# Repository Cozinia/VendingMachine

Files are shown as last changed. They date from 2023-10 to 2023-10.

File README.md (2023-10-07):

# Vending Machine

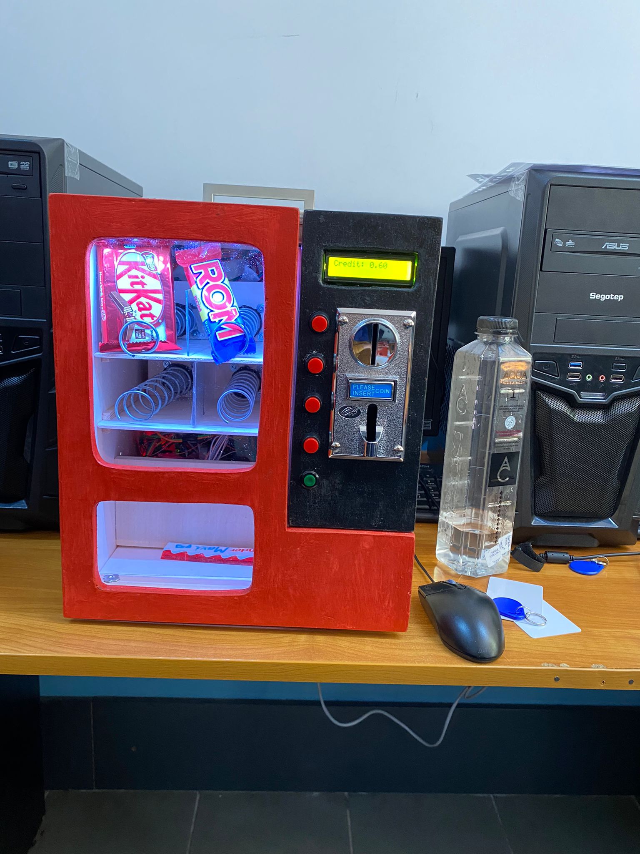
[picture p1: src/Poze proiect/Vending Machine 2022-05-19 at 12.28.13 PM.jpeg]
VendingMachinePhoto


## Descrierea componentelor folosite

În cadrul acestui proiect voi fi folosite mai multe componente așa că mai jos se află  o mică prezentare a acestora și cum sunt legate la microcontroler.
### Numărătorul de monede
Primul pe ordinea de idei este numărătorul de monede, `CH-926` pe numele de cod, acesta acceptă până la 3 tipuri diferite de monede. 
Acest modul trebuie conectat la o sursă de 12V , iar pinul ce se ocupă cu transmiterea mesajului de identificare a monedelor trebuie conectat la unul dintre pinii digitali ai microcontroler-ului ca în schema de mai jos.

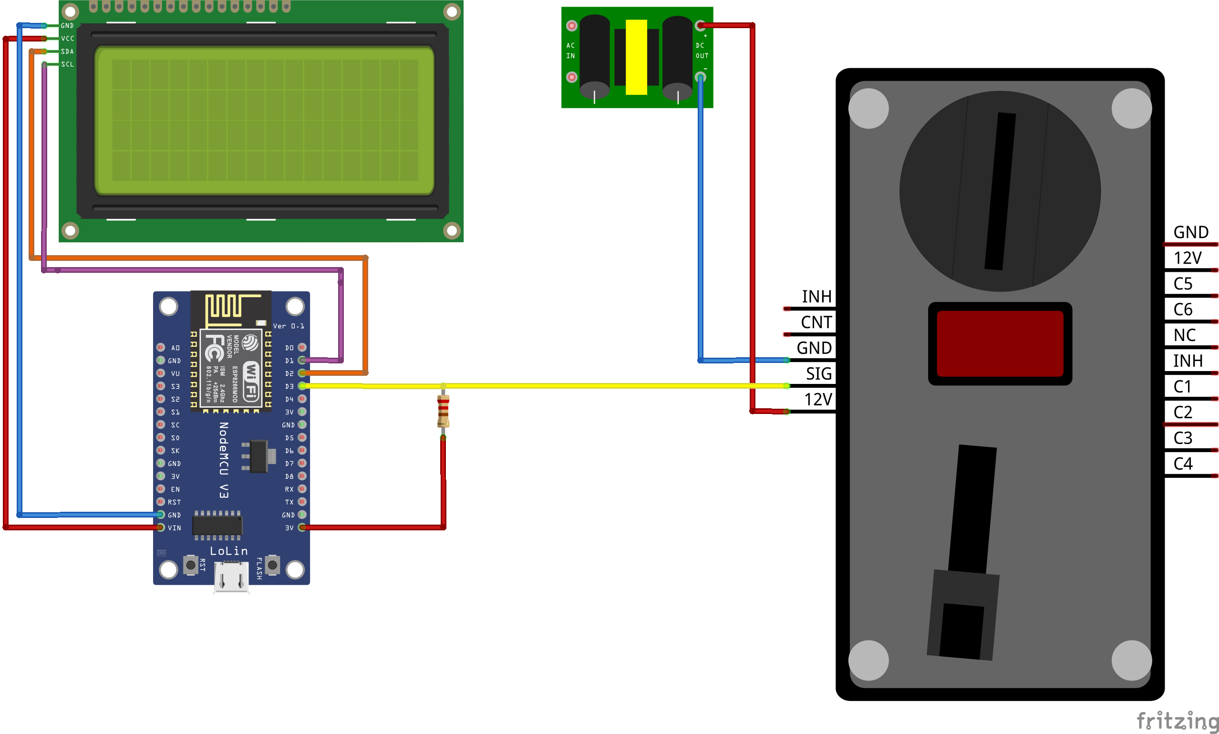
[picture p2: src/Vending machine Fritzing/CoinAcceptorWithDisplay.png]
CoinAcceptorWithDisplay


În desen se observă microcontroler-ul în partea stângă, sursa de 12V în partea de sus și numărătorul de monede în partea dreaptă.Acesta este conectat la sursa externă de 12V prin cele două fire(roșu pentru VCC și albastru pentru GND), iar prin firul de culoare galbenă la `ESP8266`, mai exact la 3V3 ce unește printr-un tranzistor pinul SIG(Coin) al acceptorului de monede cu pinul digital D3 al plăcuței.

Modulul este progrmat pentru a distinge 3 monede diferite(de `5, 10 și 50 bani`).Acesta se bazează pe pulsuri consecutive pentru fiecare tip de monedă în parte(un puls pentru 5 bani, două pulsuri pentru 10 bani, trei pulsuri pentru 50 de bani).

Iată câteva secvențe de cod interesante:

```
attachInterrupt(digitalPinToIntrerrupt(CoinPin), CoinEvent, CHANGE);
```
 
Pentru a nu supraîncărca plăcuța cu citiri successive se folosește attachInterrupt, metodă cu ajutorul căreia funcția CoinEvent este invocată doar la detectarea introducerii unei monede.
  
```
void CoinEvent()
{
    crtValue = digitalRead(CountPin);

    Serial.print("CoinEVENT_____________");
    Serial.print("\n");
    Serial.print(crtValue);
    Serial.print("\n");

}

```

`digitalRead` citește valoarea pinului Count și o stochează în variabila `crtValue`.

Funcția `Coins` se apelează în loop. Dacă timpul curent este diferit de cel anterior iar valoarea curentă de cea anterioară, timpul anterior ia valoarea celui prezent și valoarea anterioară ia valoarea celei prezente. Variabila de tip bool  numită changed își schimbă valoarea în true când această condiție este îndeplinită.Dacă diferența dintre timpul curent  și cel anterior este mai mare de 30 de milisecunde, iar changed este true, variabila number crește cu o unitate.

```
void Coins()
{
    //take current time
    crtTime = millis();
    //compare current time with previous time
    if (crtTime > prevTime)
    {
        //compare current value with previous value
        if (crtValue != prevValue)
        {
            prevTime = crtTime;

            prevValue = crtValue;
            changed = true;
        }
        if (crtTime - prevTime > 30 && changed)
        {
            counter++;
            Serial.print(counter);
            Serial.print("\n");
            changed = false;
            number++;
            Time1 = millis();
            changed = false;
        }
    }
    Time2 = millis();
    if ((Time2 - Time1 > TIMER) && (number))
    {

        Serial.print("Number: ");
        Serial.print(number);
        Serial.print("\n");
        Serial.print("Time2-Time1: ");
        Serial.print(Time2 - Time1);
        Serial.print("\n");

        if (number == 3)
        {
            credit = credit + 0.50;
            totalCoins3++;
            number = 0;
        }
        else if (number == 2)
        {
            credit = credit + 0.10;
            totalCoins2++;
            number = 0;
        }
        else
            if (number == 1)
            {
                totalCoins1++;
                credit = credit + 0.05;
                number = 0;
            }
        lcd.setCursor(0, 0);
        lcd.print("Credit: ");
        lcd.setCursor(8, 0);
        lcd.print(credit);
        Serial.print("Credit: ");
        Serial.print(credit);
        Serial.print("\n");
    }
}

```

În funcție de valoarea variabilei number, aceasta îndeplinește una dintre condițiile de mai sus.În acest fel creditul crește cu o anumită valoare(5, 10 sau 50 de bani), valoarea number este resetată la 0, iar variabila totalCoins crește cu o unitate pentru a înregistra numărul total de monede de un anumit tip.

### Display-ul

După punerea în funcțiune a numărătorului de monede a fost adăugat și un display pe care să afișeze creditul inserat.Mai jos este inserată o schemă ce conține și display-ul.

CoinAcceptorWithDisplay

Display-ul comunică prin protocolul I2C cu microcontroler-ul. Pentru a face acest lucru posibil se conectează pinii D1 la SCL(reprezentat prin cablul de culoare mov), D2 la SDA(reprezentat prin cablul de culoare oranj), pinul VIN(cel care transportă curent de 5V) la VCC și GND la GND.

```
//YWROBOT
//Compatible with the Arduino IDE 1.0
//Library version:1.1

#include <Wire.h>

#include <LiquidCrystal I2C.h>

LiquidCrystal I2C lcd(@x27, 16, 2); // set the LCD address to @x27 for a 16 chars and 2 line display

void setup()
{
lcd.init(); // initialize the lcd
i // Print a message to the LCD's screen
 lcd.backlight();

lcd.setCursor(@, 0);
lcd.print(“Atestat 2022 by");
lcd.setCursor(@, 1);
lcd.print(“Cozinia Motronu™);

}

void loop()
{

}

```
 
Acest cod folosește librăria „`LiquidCrystal_I2C`”.După declararea directivelor preprocesor „`Wire`” și „`LiquidCrystal_I2C`” se inițializează obiectul lcd care se află la adresa 0x27.În funcția setup se inițializează `lcd`, `backlight` și se setează cursorul pe poziția linia 0 și coloana 0 pentru a scrie un mesaj, respectiv lini 1 și coloana 0 pentru continuarea mesajului.
Mai jos este inserată o poză cu  un mesaj afișat pe display.

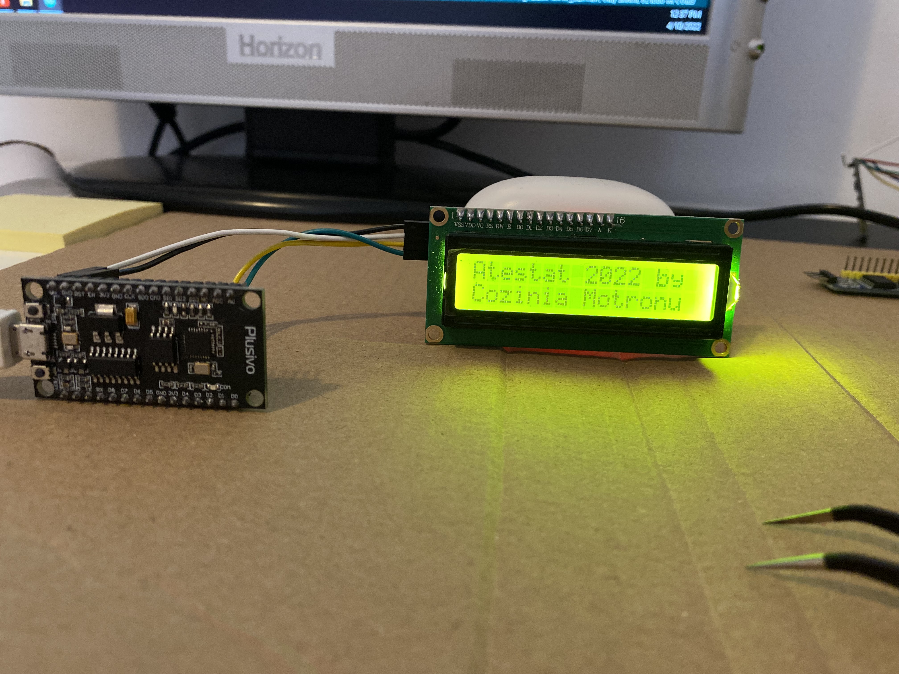
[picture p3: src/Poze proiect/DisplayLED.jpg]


### Motoarele

Acum schema începe să se încarce deoarece fiecare motor are 4 fire cu ajutorul cărora se conectează la shield-ul `CNC` și alte două care duc la modulul de expansiune `PCF8574`. Se folosesc aceste module deoarece atât motoarele, cât și celelalte componente ocupă foarte mulți pini și nu lasă loc disponibil pe microcontroler. `PCF8574` folosește același protocol precum display-ul, adică `I2C` pentru a transmite diferite evenimente ce se petrec pe pini.Acest lucru este convenabil deoarece se pot lega mai multe module de expansiune pentru a extinde numărul de pini.Aceste module se diferențiază prin adresă, fiecare putând fi programat manual ca având o anumită adresă(de la `0x20 la 0x27`) așa cum este ilustrat în imaginea de mai jos.

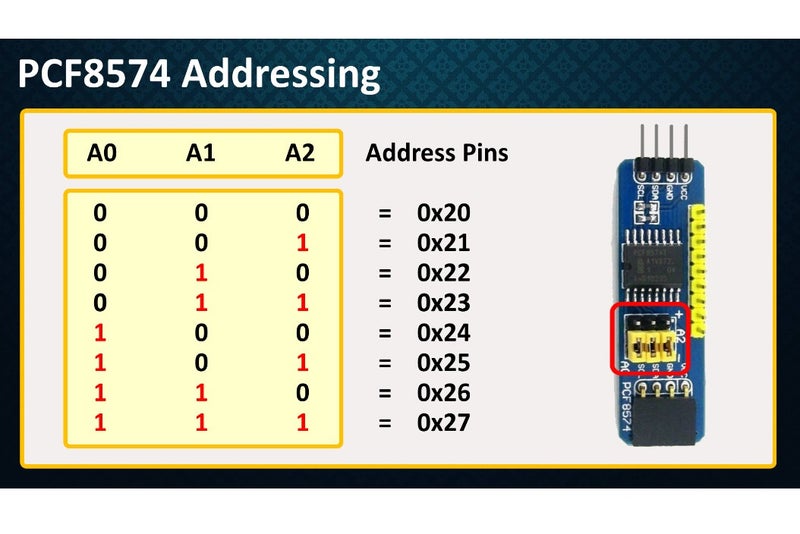
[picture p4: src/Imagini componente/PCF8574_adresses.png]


Shield-ul CNC împreună cu driver-ul de motoare `A4988` asigură buna funcționare a motoarelor oferind o interfață ușor de utilizat. 
Shield-ul oferă suport pentru maxim 4 drivere de motoare, un `pinEnable(EN)` pentru a activa mișcarea motoarelor, mai mulți pini de `ground(GND)`, pini care permit mișcarea motoarelor într-o anumită direcție și un anumit număr de pași, de exemplu: `X.STEP`(indică numărul de pași pe care motorul X să îl parcurgă), `X.DIR`(direcția în care să se învârtă motorul X). Shield-ul trebuie alimentat cu `12V` de la o sursă externă și 5V(curent necesar cerut de driver-ele de motoare).
	
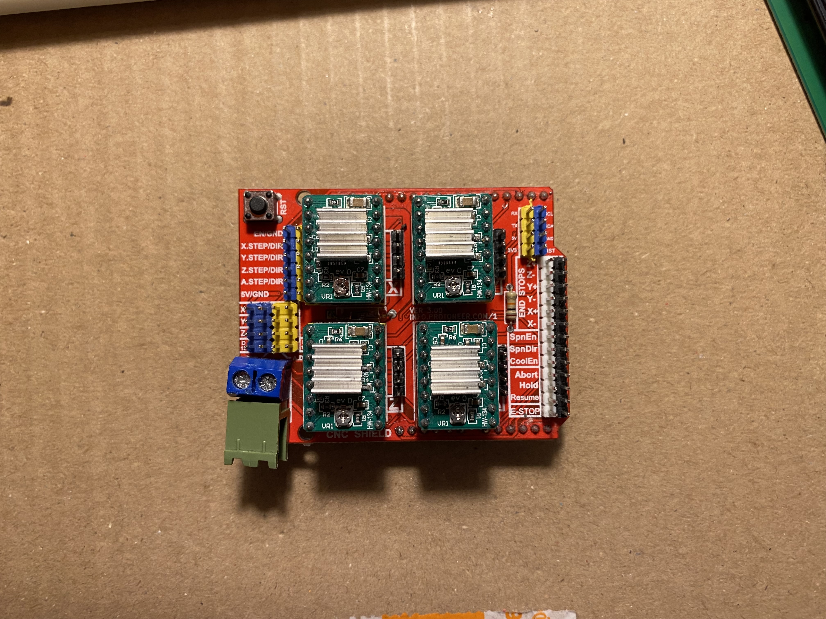
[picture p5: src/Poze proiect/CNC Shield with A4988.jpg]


Mai jos se poate observa schema proiectului la care se adaugăt motoarele, shield-ul cu driver-ele de motoare și modulele de expansiune a pinilor.

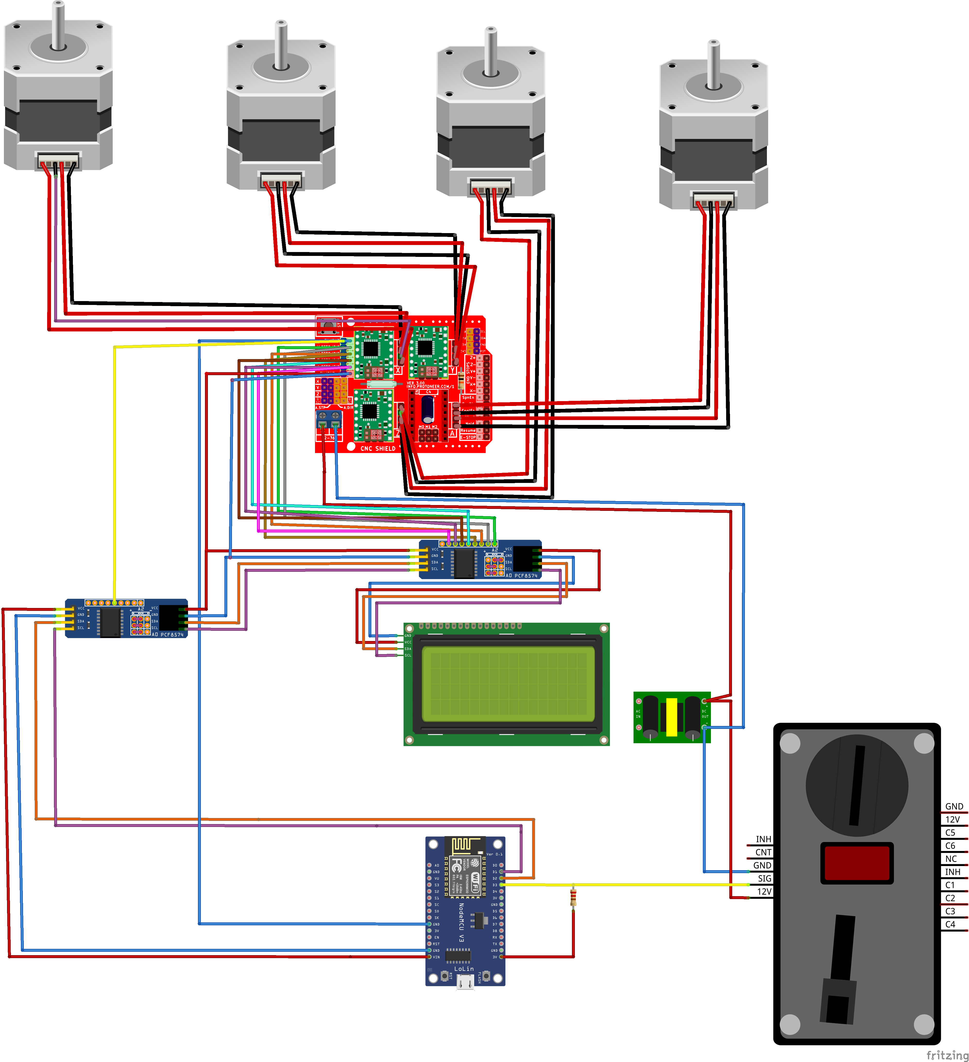
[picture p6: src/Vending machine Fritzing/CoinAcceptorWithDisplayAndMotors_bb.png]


### Modulul RFID

`RFID` este acronimul de la "radio-frequency identification" (identificare prin radiofrecvență) și se referă la o tehnologie prin care datele digitale codificate în etichete RFID sau etichete inteligente sunt captate de un cititor prin intermediul undelor radio. Tehnologia RFID este similară codului de bare, în sensul că datele de pe o etichetă sunt capturate de un dispozitiv care stochează datele într-o bază de date. Cu toate acestea, RFID are mai multe avantaje față de sistemele care utilizează un software de urmărire a activelor cu coduri de bare. Cel mai notabil este faptul că datele din etichetele RFID pot fi citite în afara liniei de vizibilitate, în timp ce codurile de bare trebuie aliniate cu un scaner optic.
Modul de utilizare este destul de simplu: utilizatorul  apropie cardul de scanner și datele sunt citite și prelucrate.În cazul acestui proiect utilizatorul folosește cardul pentru a se înregistra la vendomat, nemaifiind nevoie să introducă bani pentru a achiziționa produse.
Modulul RFID este conectat ca în schema de mai jos la pinii următori:

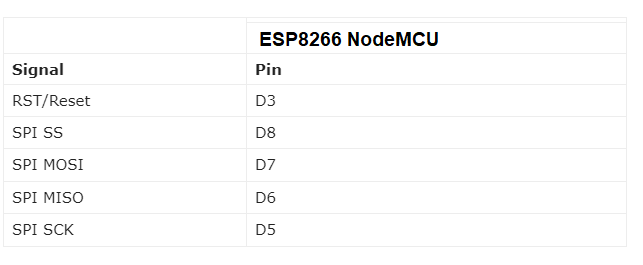
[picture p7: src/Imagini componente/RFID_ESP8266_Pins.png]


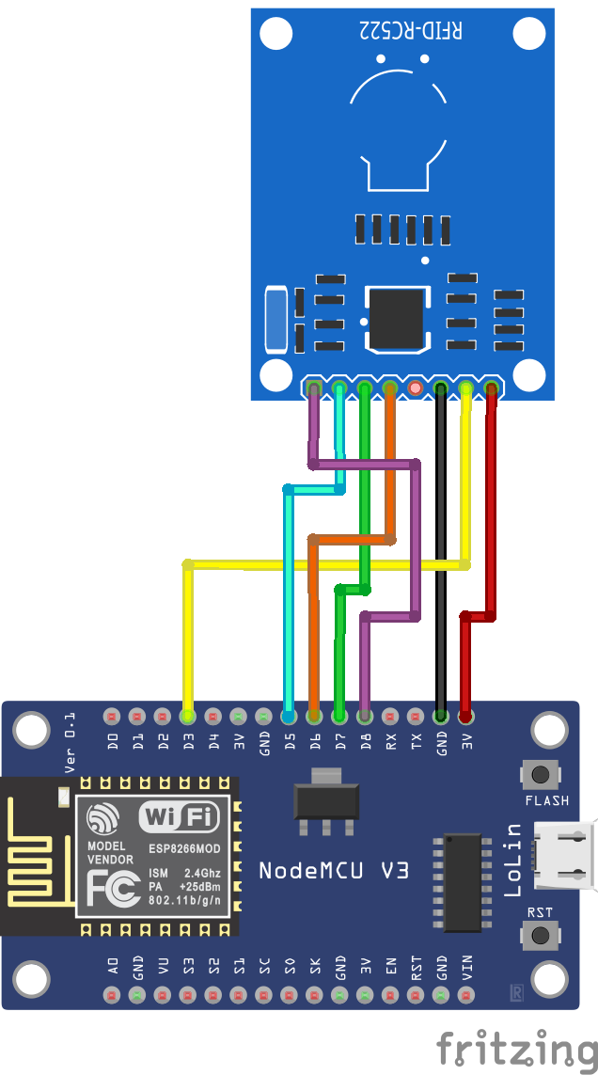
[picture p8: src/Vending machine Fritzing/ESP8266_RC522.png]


Pentru a putea folosi modulul RFID trebuie instalată librăria `MFRC522`.

Codul folosit este descris mai jos:
 
```
#include <SPI.h>
#include <MFRC522.h>

#define RST_PIN D3 // Configurable, see typical pin layout above
#define SS_PIN D8 // Configurable, see typical pin layout above
MFRC522 mfrc522(SS_PIN, RST_PIN); // Create MFRC522 instance

void setup()
{
Serial.begin(96060); // Initialize serial communications with the PC
SPI.begin(); // Init SPI bus
mfrc522.PCD_Init(); // Init MFRC522
mfrc522.PCD_DumpVersionToSerial(); // Show details of PCD - MFRC522 Card Reader details
Serial.println(F("Scan PICC to see UID, SAK, type, and data blocks..."));
}

void loop()
{
// Look for new cards
if (!mfrc522.PICC_IsNewCardPresent())
{
	return;
}
// Select one of the cards

if (!mfrc522.PICC_ReadCardSerial())
{
	return;
}
// Dump debug info about the card; PICC_HaltA() is automatically called

mfrc522.PICC_DumpToSerial(&(mfrc522.uid));

return;
}

```

După încărcarea acestui cod pe serială ar trebui să apară un mesaj asemănător cu cel de mai jos(mesajul poate să difere în funcție de versiunea moduluului RFID) unde puteți scana cardul.

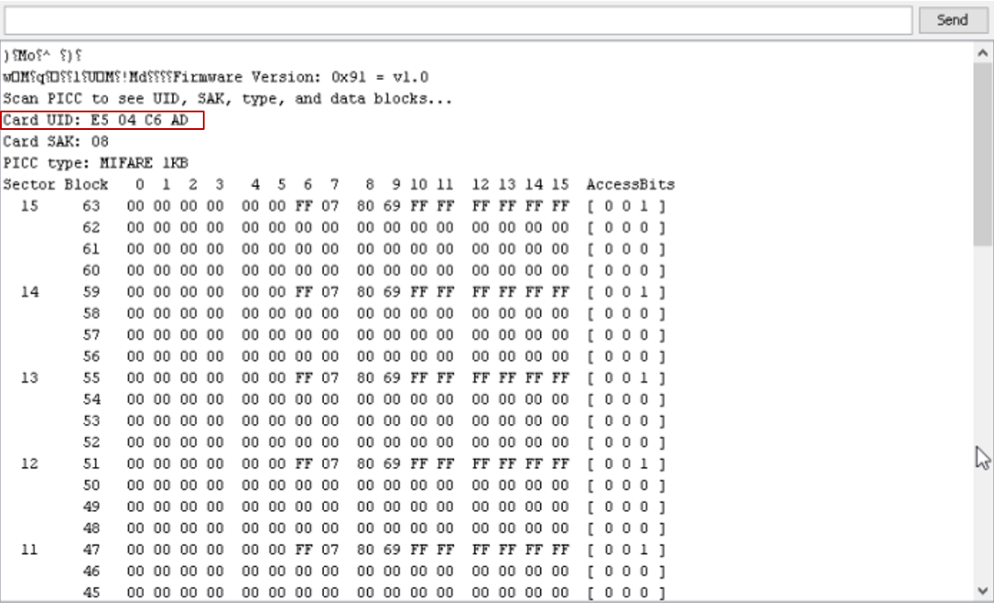
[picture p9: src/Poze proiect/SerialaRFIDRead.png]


Mai departe în implementarea codului care va identifica ID-ul cardului se va folosi „Card UID” .

### Stocarea datelor

Din cauza limitărilor spațiului de stocare pe care le au microcontroler-ele `ESP8266`(8MB RAM), nu este posibilă realizarea unei baze de date care să stocheze utilizatorii, produsele și tranzacțiile și în același timp să execute și comenzile celorlalte componente. În acest caz se folosesc structuri care imită tabelele enumerate mai sus.A cestea sunt realizate într-o clasă numită `FileDb`.

```
typedef struct
{
	char CNP[14];
	char FirstName[20];
	char Lastname[15];
	char Password[20];
	char TagNumber[15];
	float Credit;
	int isAdmin;
	int Enabled;

}User;
```

Această structură reține CNP-ul, nume, prenumele, parola, numărul cardului `RFID`, creditul, statutul utilizatorului(dacă este sau nu administrator) , iar parametrul Enabled are valoarea 1 dacă acesta este activ și 0 în caz contrar. Celelalte structuri arată similar.
După cum îi spune și numele, funcția „`AddUser()`” adaugă utilizatori. Aceasta primește ca parametru o entitate de tip User* și verifică dacă CNP-ul utilizatorului care se dorește să fie introdus se află deja în structură. Dacă da, funcția returnează 1, iar în caz contrar stochează datele noului utilizator și incrementează `userCount`. Procesul este similar pentru produse și tranzacții.

```
int FileDb::AddUser(User* entity)
{
	bool exists = false;
	for (int i = 0; i < this->userCount; i++)
	{
		if (strcmp(entity->CNP, this->users[i].CNP)==0)
		{
			exists = true;
			return 1;
		}
	}

	this->users[this->userCount] = *entity;
	this->userCount++;
	//SaveAll();
	return 0;
}
```

În funcția `InitData` sunt creați câțiva utilizatori, produse și tanzacții urmând modelul din figurile inserate mai jos.

```
void FileDb::InitData()
{
	
	User user1;
	strcpy(user1.CNP, "19712073264");
	strcpy(user1.Password, "abc");
	strcpy(user1.FirstName, "Ion");
	strcpy(user1.LastName, "Vasilescu");
	strcpy(user1.TagNumber, "89178228185");
	user1.isAdmin = 1;
	user1.Enabled = 1;
	user1.Credit = 2.40;
	AddUser(&user1);

	Product product1;

	product1.ID = 1;
	strcpy(product1.Name, "Snikers");
	product1.Position = 3;
	product1.Price = 1.5;
	product1.Enabled = 1;
	product1.Quantity = 5;
	AddProduct(&product1);

}
```

### Aplicația web
	
Aplicația web este construită folosind `HTML`, `CSS` și `VueJS`. Din cauza spațiului mic de stocare al microcontroler-ului această aplicație web este construită pe o singură pagină.
Primul element care va apărea în pagină este formularul de logare.În acest formular utilizatorul va introduce CNP-ul și parola.Prin apăsare butonului `Login` se va apela funcția `LogIn()`.

```
 <div id="app" v-model="StartUp()" v-cloak>
        <!--Login page-->
        <div id="Menu2" v-if="!UserIsLogged">
            <div style=" margin: 150px 0px 0px 0px; text-align: center;">
                <h1 style="text-align:center;">Login form</h1>
                <form class="ui form">
                    <div class="field">
                        <label>Username</label>
                        <input type="text" id="username" placeholder="Username">
                    </div>
                    <div class="field">
                        <label>Password</label>
                        <input type="text" id="password" placeholder="Password">
                    </div>
                    <button class="ui button" type="button" v-on:click="LogIn()"><p>Login</p></button>
                </form>
            </div>
        </div>

```

```
 async LogIn() {
            var username = document.getElementById("username").value;
            var password = document.getElementById("password").value;      
            var url = encodeURI("/LogIn" + "?" + "Username=" + username + "&" + "Password=" + password);
            var result = await fetch(url);   
            if (result.status == 200) {
                this.UserInfo.Data = await result.json();
                if (!this.UserInfo.Data[0].isAdmin) {
                    this.UserIsLogged = true;
                    this.isAdmin = true;
                    alert("Welcome back, " + this.UserInfo.Data[0].FirstName + "!");  
                } else if (this.UserInfo.Data[0].isAdmin) {
                    this.UserIsLogged = true;
                    this.isAdmin = false;
                    alert("Welcome back, " + this.UserInfo.Data[0].FirstName + "!");
                } 
            }else {
                this.UserInfo.Error.Message = await result.json();
                alert(this.UserInfo.Error.Message);
                this.UserIsLogged = false;
                this.isAdmin = false;
            }                 
        }
```

Această funcție este de tip `async` deoarece așteaptă rezultatul de la server. Datele introduse de utilizator sunt aduse aici prin instrucțiunea `document.getElementById`. Acestea sunt trimise la server și interpretate.

```
int LogIn()
{
	String cnp = server.arg("Username");
	String pwd = server.arg("Password");	
	User* user = fileDb.GetUserByCNP((char*)cnp.c_str());
	if (user != NULL)
	{
		if (strcmp(user->Password, pwd.c_str()) == 0)
		{
			sprintf(MyBuffer, "[{\"CNP\":\"%s\", \"FirstName\": \"%s\", \"LastName\":\"%s\", \"isAdmin\": %d, \"Credit\": %f,\"TagNumber\": %ld, \"isActive\": %d}]", user->CNP, user->FirstName, user->LastName, user->isAdmin, user->Credit, user->TagNumber, user->Enabled);
			server.send(200, "application/json", MyBuffer);
		}
		else
		{
			server.send(601, "text/plain", "Invalid CNP or password");
		}
	}
	server.send(602, "text/plain", "User doesn't exist!");
	return 1;
}
```

Această funcție se află pe server și interpretează datele introduse. Acestea sunt preluate din aplicația web prin instrucțiunea `server.arg(„ExNume”)`.Variabila user de tip `User*` stochează răspunsul funcției `GetElementByCNP` aflată în clasa `FileDb`.

```
User* FileDb::GetUserByCNP(char* cnp)
{
	
	for (int i = 0; i < this->userCount; i++) {
		if (strcmp(cnp, this->users[i].CNP)==0) {
			
			return &this->users[i];
		}
	}
	return NULL;
}
```

Această funcție verifică dacă parametrul `cnp`  corespunde utilizatorului `users[i]`. În caz afirmativ returnează datele utilizatorului, iar în caz contrar `NULL`.

În funcția `LogIn` se verifică dacă parola utilizatului primit anterior corespunde cu cea trimisă din aplicația web. În caz afirmativ datele se formatează în format `json` folosind funcția `sprintf` și se trimit în pagina web ca răspuns alături de codul 200(ok). În caz contrar se trimite codul de eroare 601(acest cod este creat de mine și înseamnă „CNP sau parolă invalidă”).În cazul în care nici parola și nici CNP-ul nu se potrivesc cu datele existente deja se trimite codul de eroare 602(utilizatorul nu există).

Dacă CNP-ul și parola se potrivesc, pe client se primește codul 200(ok) și se verifică dacă utilizatorul este administrator sau nu.În acest afirmativ, variabila de tip bolean isAdmin ia valoarea true, în caz contrar ia valoarea false. În ambele dintre aceste cazuri este afișat mesajul „Welcome back” urmat de numele utilizatorului.În caz că datele introduse nu se potrivesc celor existente în structură se va afișa mesajul venit de la server stocat în `UserInfo.Error.Message`.

După ce utilizatorul a fost logat variabila de tip bolean `UserIsLogged`  ia valoarea true, iar în funcție de valoarea variabilei isAdmin se afișează meniul administratorului sau al utilizatorului.

### Meniul administratorului
Mai jos este inserată  o captură de ecran reprezentând structura paginii administratorului.Acesta poate vedea lista utilizatorilor și a produselor, poate adăuga utilizatori și produse, poate deschide ușa vendomatului și nu în ultimul rând, poate testa funcționalitatea motoarelor.

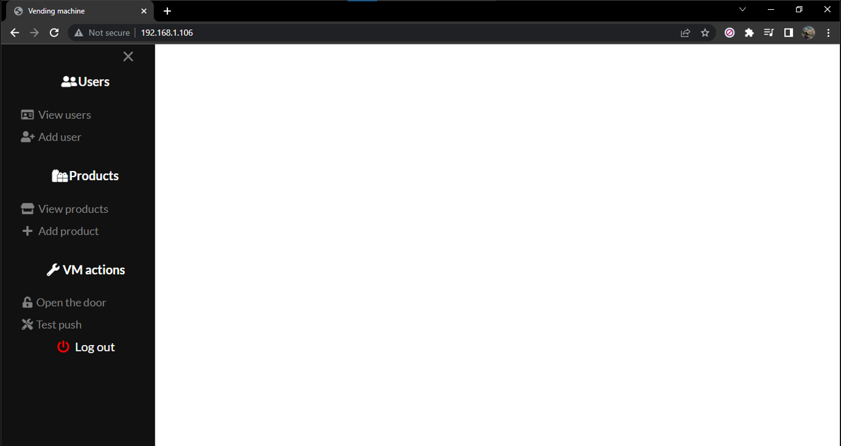
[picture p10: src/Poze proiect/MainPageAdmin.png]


Meniul de vizualizare a utilizatorilor afișează toți utilizatorii și informațiile acestora.În acest meniu administratorul poate edita datele acestora și îi poate dezactiva.
	
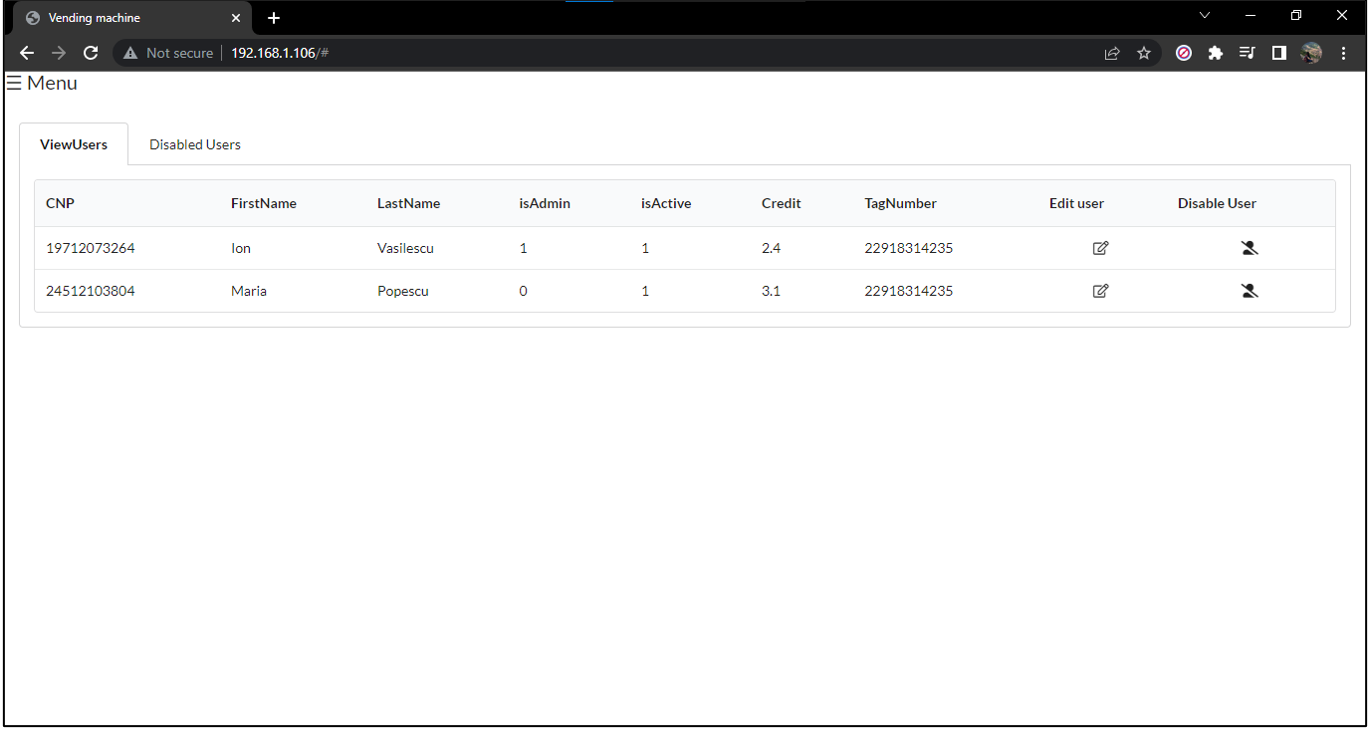
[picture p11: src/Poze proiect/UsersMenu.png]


Pentru a face acest lucru posibil, la apăsarea butonului `ViewUsers` se apelează funcția `GetUsers`.

```
 async GetUsers() {
	const responseUsers = await fetch("/Users");
	this.UserInfo.Users = await responseUsers.json();
	this.users = this.UserInfo.Users;
	
}
```

Această funcție se conectează la funcția `Users` din server și preia datele tuturor utilizatorilor existenți precum este prezentat în imaginea de mai jos.

```
void Users() {
	MyBuffer[0] = NULL;
	TempBuffer[0] = NULL;
	strcat(MyBuffer, "[");
	for (int i = 0; i < fileDb.userCount; i++)
	{
		Serial.print(MyBuffer);
		sprintf(TempBuffer, "{\"CNP\":\"%s\", \"FirstName\": \"%s\", \"LastName\":\"%s\", \"isAdmin\": %d, \"Credit\": %f,\"TagNumber\": \"%s\", \"isActive\": %d}", fileDb.users[i].CNP, fileDb.users[i].FirstName, fileDb.users[i].LastName, fileDb.users[i].isAdmin, fileDb.users[i].Credit, fileDb.users[i].TagNumber, fileDb.users[i].Enabled);
		if (i < fileDb.userCount - 1)
		{
			strcat(MyBuffer, TempBuffer);
			strcat(MyBuffer, ",");
		}
		else
		{
			strcat(MyBuffer, TempBuffer);
		}
	}
	strcat(MyBuffer, "]");
	server.send(200, "application/json", MyBuffer);
}
```

Informațiile utilizatorilor sunt formatate în format `json` în funcția `snprintf` în variabila de tip char `TempBuffer`.După care se pune o virgulă între datele utilizatorilor și se concatenează în variabila de tip char `MyBuffer` folosind funcția `strcat`.La final se trimite variabila `MyBuffer` în aplicația web și codul 200. Acestea sunt afișate pe ecran într-un tabel.

```
                <!--If the "ViewProducts" button was pressed this div will be displayed on screen-->
                <div class="ui basic segment" v-if="Menu.ViewProducts">
                    <div id="ShowSubmenuProducts">
                        <div class="ui top attached tabular menu">
                            <a class="item active" v-on:click="ShowSubmenuProducts('ViewProductsMenu')" id="ViewProducts">
                                View Products
                            </a>
                            <a class="item" v-on:click="ShowSubmenuProducts('DisableProductsMenu')" id="DisableProducts">
                                Disabled products
                            </a>

                        </div>
                        <div class="ui bottom attached segment" v-if="ProductsSubmenu.DisableProductsMenu">
                            <div class="row">
                                <table class="ui unstackable table">
                                    <thead>
                                        <tr>
                                            <th>ID</th>
                                            <th>Name</th>
                                            <th>Quantity</th>
                                            <th>Position</th>
                                            <th>Price</th>
                                            <th>isActive</th>
                                            <th>Edit product</th>
                                            <th>Enable product</th>
                                        </tr>
                                    </thead>
                                    <tbody v-for="product in products">                                        
                                        <tr v-if="!product.isActive">
                                            <td>{{product.ID}}</td>
                                            <td>{{product.Name}}</td>
                                            <td>{{product.Quantity}}</td>
                                            <td>{{product.Position}}</td>
                                            <td>{{product.Price}}</td>
                                            <td>{{product.isActive}}</td>
                                            <td style="text-align:center"><i class="edit outline icon disabled"></i></td>
                                            <td style="text-align:center"><i class="ban icon" v-on:click="EnableProduct(product)"
                                                 style="color:red;"></i></td>
                                        </tr>
                                    </tbody>
                                </table>
                            </div>
                        </div>

```

Apăsând iconița de edit se va deschide modal-ul de mai jos în care se pot edita informațiile utilizatorului.

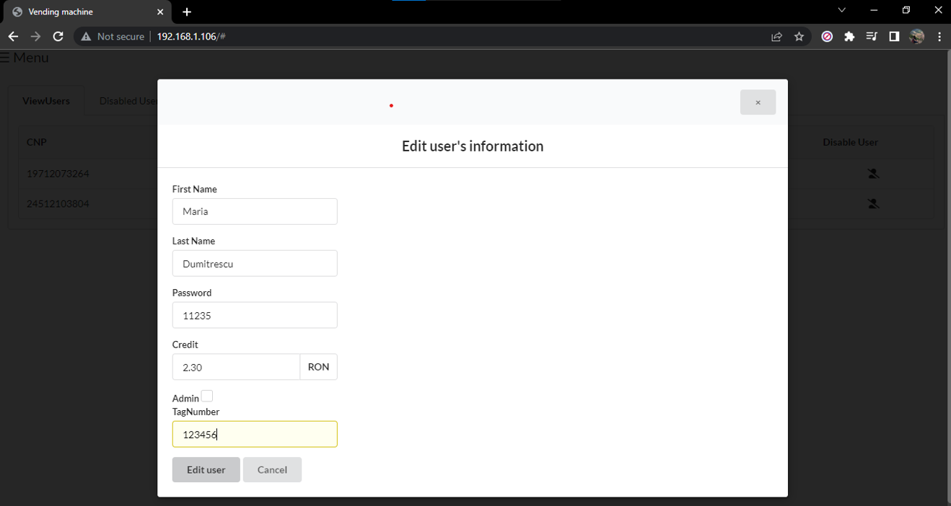
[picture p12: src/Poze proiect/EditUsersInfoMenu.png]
 

Prin apăsarea butonului aceste informații ajung în funcția `EditUser` de unde sunt trimise pe server unde sunt prelucrate.Dacă prelucrarea s-a putut face atunci serverul va returna codul 200, în caz contrar va returna un cod de eroare.

```
async EditUser() {
            var toEditFirstName = document.getElementById("FirstName-modal").value;
            var toEditLastName = document.getElementById("LastName-modal").value;
            var toEditPassword = document.getElementById("Password-modal").value;
            var toEditCredit = document.getElementById("Credit-modal").value;
            var toEditAdmin = document.getElementById("CheckIfAdmin-modal");
            if (toEditAdmin.checked == true) {
                toEditAdmin = 1;
            } else {
                toEditAdmin = 0;
            }
            var toEditTagNumber = document.getElementById("TagNumber-modal").value;
            var CNP = this.TempUserEdit.CNP;
            if (toEditFirstName != "" && toEditLastName != "" && toEditCredit != "" &&  toEditTagNumber != "") {
                var editUrl = encodeURI("/EditUsers" + "?" + "CNP=" + CNP + "&" + "toEditFirstName=" 
                + toEditFirstName + "&" + "toEditLastName=" + toEditLastName + "&" + "toEditPassword=" 
                + toEditPassword + "&" + "toEditCredit=" + toEditCredit + "&" + "toEditAdmin=" + toEditAdmin + "&" 
                + "toEditTagNumber=" + toEditTagNumber);
                var editResult = await fetch(editUrl);
                console.log(editResult.status);
                if (editResult.status == 200) {
                    this.ShowModal("User's info has been updated!");
                }
                else {
                    this.ShowModal("Couldn't update user's info!");
                }
            } else {
                this.ShowModal("Fill all fields before submitting the form!");
            }
            this.GetUsers();
            $('.modal')
                .modal('hide')
                ;
            
        }
```

Mai jos este inserată o captură de ecran cu un exemplu de date ce pot fi inserate în câmpurile meniului de adăugarea a utilizatorilor.

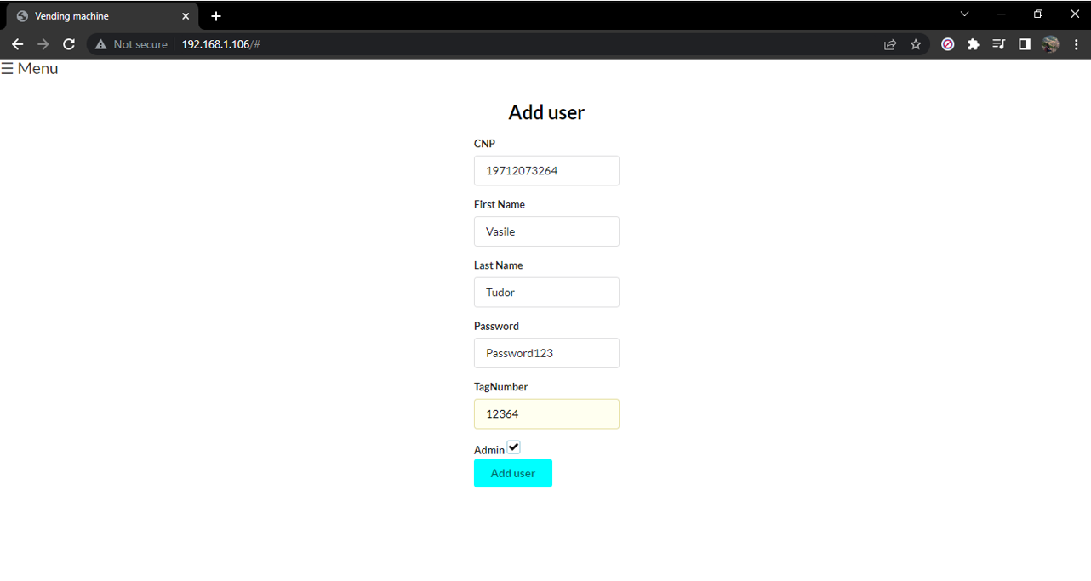
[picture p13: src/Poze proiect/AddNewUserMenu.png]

 
Adăugarea utilizatorilor se face trimițând datele inserate în formularul de mai jos pe server unde se execută funcția `AddUser` prezentată mai sus.

### Modul de funcționare al vendomatului

Modul de funcționare de bază:
Clientul introduce monede în vendomat, selectează produsul dorit, iar vendomatul returnează produsul.
Cum funcționează procesul de selecție:
* Butonul a fost apăsat
* Se verifică stocul produsului
* Se verifică dacă creditul inserat de utilizator este suficient pentru produsul selectat
* În cazul în care toate condițiile au fost îndeplinite vendomatul returnează produsul clientului
Vendomatul suportă 3 tipuri de monede(5, 10 și 50 de bani), 4 tipuri de produse din care utilizatorul poate alege și două moduri: standard și company.
În modul standard clientul inserează monede în vendomat, vede creditul introdus pe ecran, selectează produsul dorit , iar vendomatul îl returnează.
Pentru a vedea aplicația web din modul company este necesară conectarea la aceeași rețea ca cea a vendomatului.
În modul company utilizatorul scanează cardul RFID  pentru a se autentifica, selectează produsul dorit , iar vendomatul îl returnează.În acest mod de funcționare utilizatorul are un cont la care se poate loga și unde poate vedea tranzacțiile făcute și creditul rămas.
Modul de funcționare a sistemului de logare cu cardul RFID:
* Utilizatorul scanează cardul
* Un mesaj este afișat pe ecran
* După 3 secunde pe ecran este afișat creditul
* Începe procesul de selecție prezentat mai sus
* După terminarea procesului de selecție clientul apasă buton de logout 

Modul company vine și cu un cont de administrator unde acesta poate vedea, edita sau adăuga utilizatori și produse și nu în ultimul rând, poate testa funcționalitatea motoarelor.

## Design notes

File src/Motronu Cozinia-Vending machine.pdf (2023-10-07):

## LICEUL TEORETIC ”BENJAMIN FRANKLIN”

## București, Sector 3

# VENDING MACHINE

## Elev:

## Motronu Ioana-Cozinia

## Profesor îndrumător:

## Niculescu Mihaela-Carmen

## Mai, 2022

## CUPRINS

## Motivarea alegerii temei

Încă de când eram foarte mică am avut o pasiune pentru partea tehnică a lucrurilor și

mi-a plăcut să creez diferite lucruri.Visul meu era să devin inventator, când am crescut mi-am

dat seama că trebuie să învăț fizică pentru a face acest lucru posibil.

Povestea acestui vendomat se învârte în jurul numărătorului de monede, ideea de

vendomat venind de aici.Mai întâi am făcut posibilă afișarea pe un ecran a numărului de monede

introduse și valoarea acestora, apoi am introdus motoarele acționate de butoane atunci când creditul este mai mare sau egal cu o valoare prestabilită de mine.În luna octombrie a anului

trecut(2021) aproape terminasem proiectul, însă m-am gândit că ar fi mult mai interesant dacă

aș adăuga o aplicație web din care utilizatorii să își poată vedea creditul rămas și produsele

achiziționate.Deși pare destul de simplu la prima vedere, acest lucru mi-a dat mari bătăi de cap

deoarece a trebuit să implementez o bază de date locală pe memoria dispozitivului(EEPROM)

și să lucrez cu tehnologii noi pentru mine precum Vuejs, Fomantic-cadru de dezvoltare a

diverselor machete receptive, SQLite sau ASP.NET Core în care am simulat serverul de pe

dispozitiv.

## Descrierea limbajelor folosite

Complexitatea acestui proiect nu este dată doar de multitudinea de componente fizice

pe care le utilizează, ci și de limbajele de programare folosite.Programul principal este construit

în Arduino, un subset al programului C++.Acestuia i se adaugă o bază de date în SQLite și o

aplicație web ce folosește HTML, CSS, JavaScript și Vue.js.

Am separat acest proiect în trei părți pentru a fi mult mai ușor de construit.Prima dată

am realizat vendomatul fizic.Acest lucru presupune punerea laolaltă a componentelor, cablarea

acestora și construirea unui program care permite bun funcționare simbiotică a acestora.Deși nu a fost deloc ușor, am reușit să fac acest lucru posibil.În folderul proiectului se află câteva

videoclipuri cu motoarele, display-ul și cum funcționează vendomatul.

În cea de-a doua parte am creeat o bază de date în SQLite.Cu ajutorul acesteia am reușit

să stochez informații legate de utilizatori și tranzacțiile acestora, însă mai multe pe această temă

la capitolul „Descrierea bazei de date”.

În ultima dar nu cea din urmă parte am construit o aplicație web ce folosește HTML,

CSS, JavaScript și Vue.js. Descoperirea unui framework precum Fomantic (https://fomantic-ui.com/) mi-a fost de mare

ajutor deoarece nu am construit de la zero interfața web.Acesta conține o multitudine de

elemente gata construite ce așteaptă să fie folosite, însă acestea au nevoie de implementare

JavaScript și Vue.js pentru a funcționa în parametrii.

Pentru o scurtă perioadă de timp am folosit ASP.NET CORE pentru a simula serverul

de pe dispozitiv.Am ales acest web framework deoarece oferă flexibilitate și un timp de răspuns

mai bun comparativ cu ESP8266, acest server fiind creat direct pe laptopul meu în comparație cu serverul plăcuței pe care o folosesc în proiect.Însă mai multe despre acest framework puteți

găsi în capitolul „Noțiuni elementare în ASP.NET CORE”.

Pentru fiecare dintre aceste părți am pregătit câte un capitol separat însoțit de explicații

de la 0 pentru a vă putea ajuta să înțelegeți acest proiect fără experiențe anterioare în acest

domeniu.

## Noțiuni de bază în limbajul C++

Noțiuni introductive

C++ (numit C plus plus) este un limbaj de programare orientat pe obiecte creat de

informaticianul Bjorne Stroustrop ca parte a evoluției familiei de limbaje C. A fost dezvoltat ca

o îmbunătățire multiplatformă a C pentru a oferi dezvoltatorilor un grad mai mare de control

asupra memoriei și a resurselor sistemului.

Unii numesc C++ „C cu clase” deoarece introduce principii de programare orientată pe

obiecte, inclusiv utilizarea unor clase definite, în cadrul limbajului de programare C. De-a

lungul timpului, C++ a rămas un limbaj foarte util nu numai în programarea computerelor în

sine, ci și în predarea noilor programatori despre cum funcționează programarea orientată pe

obiecte. Cu toate acestea, nu suportă doar orientat pe obiecte, ci și procedural și funcțional.

Datorită flexibilității și scalabilității sale ridicate, C++ poate fi utilizat pentru a dezvolta o gamă

largă de software, aplicații, browsere, interfețe grafice cu utilizatorul (GUI), sisteme de operare

și jocuri.

Astăzi, C++ este încă foarte apreciat pentru portabilitatea sa notabilă, care permite

dezvoltatorilor să creeze programe care pot rula pe diferite sisteme de operare sau platforme foarte ușor. În ciuda faptului că este un limbaj de nivel înalt, deoarece C++ este încă aproape

de C, poate fi folosit pentru manipulare la nivel scăzut datorită relației sale strânse cu limbajul

mașină.

Care a fost scopul creării acestui limbaj?

Bjarne Stroustrup a dezvoltat C++ la Bell Labs la începutul anilor 1980 pentru a îmbina

cele mai bune avantaje ale mai multor alte limbaje de programare. El a vrut să combine

rapiditatea BCPL, nivelul înalt al Simula și universalitatea lui Dennis Ritchie C. S-a inspirat și

din alte limbi, cum ar fi Ada, ML și ALGOL 68, pentru a crea un program bine structurat. ,

limbaj de uz general care ar putea compila aproape toate programele C fără a-și schimba codul

sursă. C++ este atât de flexibil încât este adesea supranumit „Cuțitul de buzunar elvețian al

limbajelor de programare” (deși această poreclă este împărtășită și de Python).

## Structura unui program C++

Deoarece este un limbaj proiectat în limba engleză, C++ folosește doar litere mari și mici ale alfabetului englez, cifre(0,1,2,...,9), set de caractere „ + - * / ( ) { } @ $ ”.La scrierea liniilor într-un program C++ se folosesc anumite caractere speciale denumite separatori precum spațiu „ ”, „ ; ” folosit ca separator de linie în program, „ , ” utilizat cu scopul de a separa elemente ale unui șir.Comentariu este un element ajutător pentru a scrie anumite explicații într-o linie de program folosind semnul backslash dublu „ // ”, sau pe mai multe linii de cod folosind backslash și steluță la începutul și sfârșitul comentariului „ /* acesta este un comentariu */ ”.

Orice program este alcătuit din una sau mai multe module numite funcții.Este obligatoriu ca orice program să conțină funcția principală „main()”.Aceste paranteze pot conține parametrii formali (constante sau variabile) sau nimic.Întotdeauna perechea de acolade se va scrie sub cuvântul „main” și va conține declarații ale variabilelor locale și instrucțiuni specifice programului.

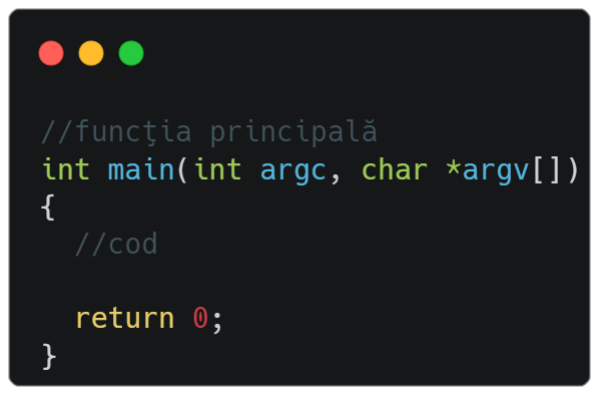
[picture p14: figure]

În figura de mai sus am scris un program C++ care returnează 0.Cuvântul scris în fața lui main reprezintă tipul valorii calculate și returnate în funcția main.Programele C++ au o structură standard:directive preprocesor, variabile globale, funcții.

Directivele preprocesor se scriu la începutul fiecărui program astfel „#include <iostream>”.Această directivă preprocesor utilizează diferite biblioteci pentru a citi și a afișa informația. În programare, nu putem avea variabile, funcții etc. cu același nume. De aceea, pentru a evita aceste conflicte, folosim un namespace. Deci, pentru un namespace putem avea un nume unic și același nume poate fi folosit și într-un alt namespace.

Valorile pe care le folosim de-a lungul unui program pot fi constante sau variabile.Acestea se pot declara inițial „#define pi 3.14”, înaintea lui main și se numesc declarări globale deoarece se pot folosi în toate funcțiile programului, sau local într-una dintre funcții.Acestea sunt de mai multe tipuri precum int (valoare întreagă), float (valoare reală), bool (poate avea valoarea doar true sau false), char (reține un caracter) etc.Aceste valori suportă diferite operații matematice precum atribuirea, adunarea sau scăderea.

Operatorii limbajului C++ sunt:

1. Matematici: +, - , *, /,
2. Relaționali: <, >, <=, >=, ==, !=
3. Logici: !(negație), &&(și), || (sau)

Folosind informațiile enunțate mai sus se poate construi un program C++ simplu care afișează pe ecran un mesaj.

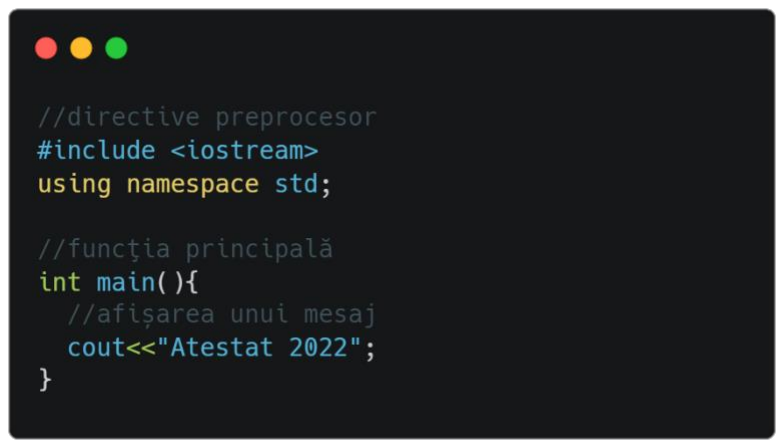
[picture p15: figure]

## Noțiuni de bază în Arduino C++

Proiectul Arduino a fost demarat la Institutul de Interaction Design Ivrea (IDII) din Ivrea, Italia. La acea vreme, studenții foloseau un microcontroler BASIC Stamp la un cost de 200 de lei. În 2003, Hernando Barragán a creat platforma de dezvoltare Wiring ca proiect de teză de masterat la IDII, sub supravegherea lui Massimo Banzi și Casey Reas. Casey Reas este cunoscut pentru că a creat, împreună cu Ben Fry, platforma de dezvoltare Processing. Scopul proiectului a fost acela de a crea instrumente simple și cu costuri reduse pentru crearea de proiecte digitale de către cei care nu sunt ingineri.

Platforma Wiring era compusă dintr-o placă de circuite imprimate (PCB) cu un microcontroler ATmega128, un IDE bazat pe Processing și funcții de bibliotecă pentru a programa cu ușurință microcontrolerul. În 2005, Massimo Banzi, împreună cu David Mellis, un alt student IDII, și David Cuartielles, au extins Wiring prin adăugarea suportului pentru microcontrolerul ATmega8, mai ieftin. Noul proiect, bifurcat din Wiring, s-a numit Arduino.

Hardware-ul original Arduino a fost fabricat de compania italiană Smart Projects.Unele plăci Arduino au fost proiectate de companiile americane SparkFun Electronics și Adafruit Industries. Începând cu 2016, au fost produse în comerț 17 versiuni ale hardware-ului Arduino.

Arduino este un subset al limbajului C++ ce se bazează pe cablarea fizică a componentelor. Este o istorie lungă de proiecte bazate pe alte proiecte, într-un mod foarte deschis. IDE-ul Arduino este compus din două medii, IDE-ul de procesare și IDE-ul de cablare.

În lucrul cu Arduino se folosește în mod obișnuit Arduino IDE (Integrated Development Environment), un software disponibil pentru toate platformele desktop majore (macOS, Linux, Windows), care ne oferă două lucruri: un editor de programare cu suport pentru biblioteci integrate și o modalitate de a compila și de a încărca ușor programele Arduino pe o placă conectată la computer.

Arduino este mai exact o platformă de electronice open-source ce se bazează pe hardware și software.Plăcile dezvoltate de Arduino sun capabile de citirea unor input-uri precum apăsarea unui buton și transformarea acestora în output-uri precum aprinderea unui led.Toate aceste lucruri sunt posibile prin transmiterea unui set de instrucțiuni microcontroler-ului de la bordul plăcuței.

Instalarea IDE-ului Arduino?
Pentru a instala Arduino IDE este necesară accesarea acestui link https://www.arduino.cc/en/software și descărcarea unei versiuni potrivite sistemului de operare.

După descărcare se urmează procesul de instalare de tip „Next->Next” asemănător cu cel din imaginile următoare:

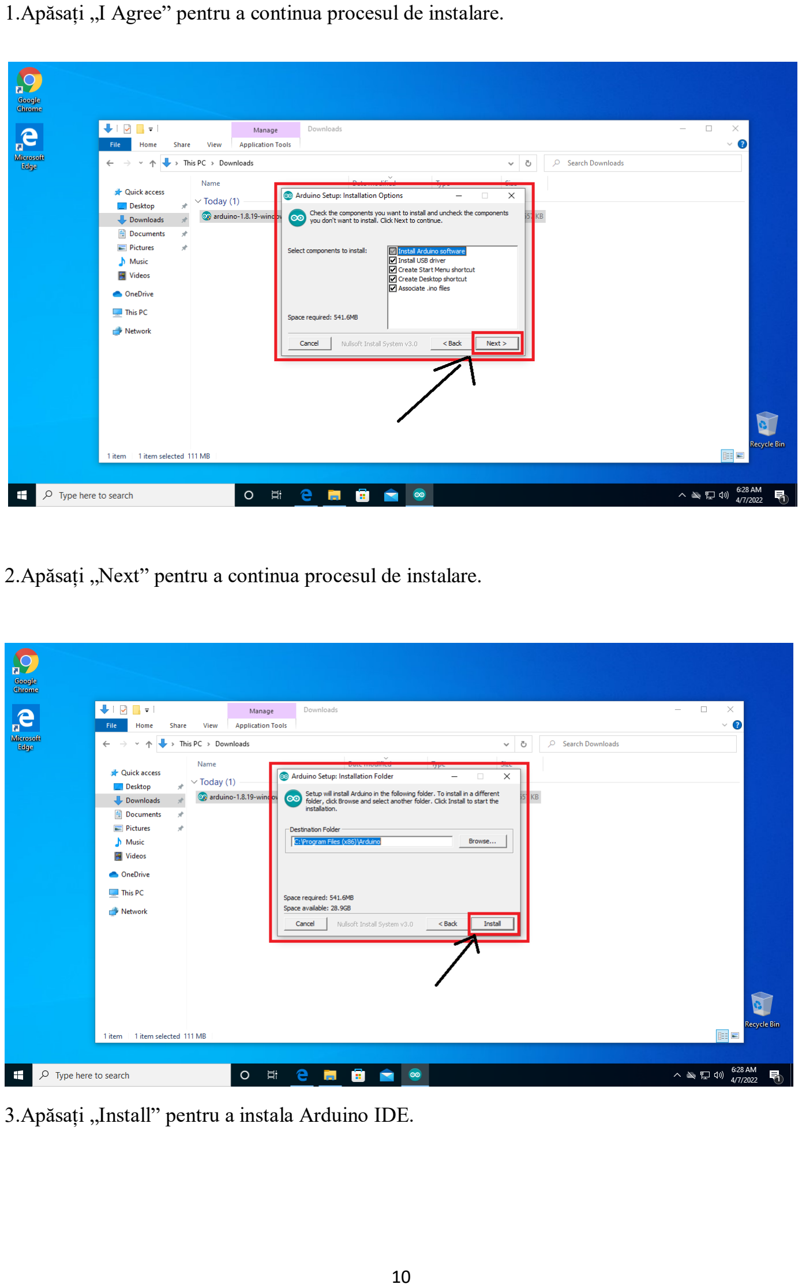
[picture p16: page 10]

1.Apăsați „I Agree” pentru a continua procesul de instalare.

2.Apăsați „Next” pentru a continua procesul de instalare.

3.Apăsați „Install” pentru a instala Arduino IDE.

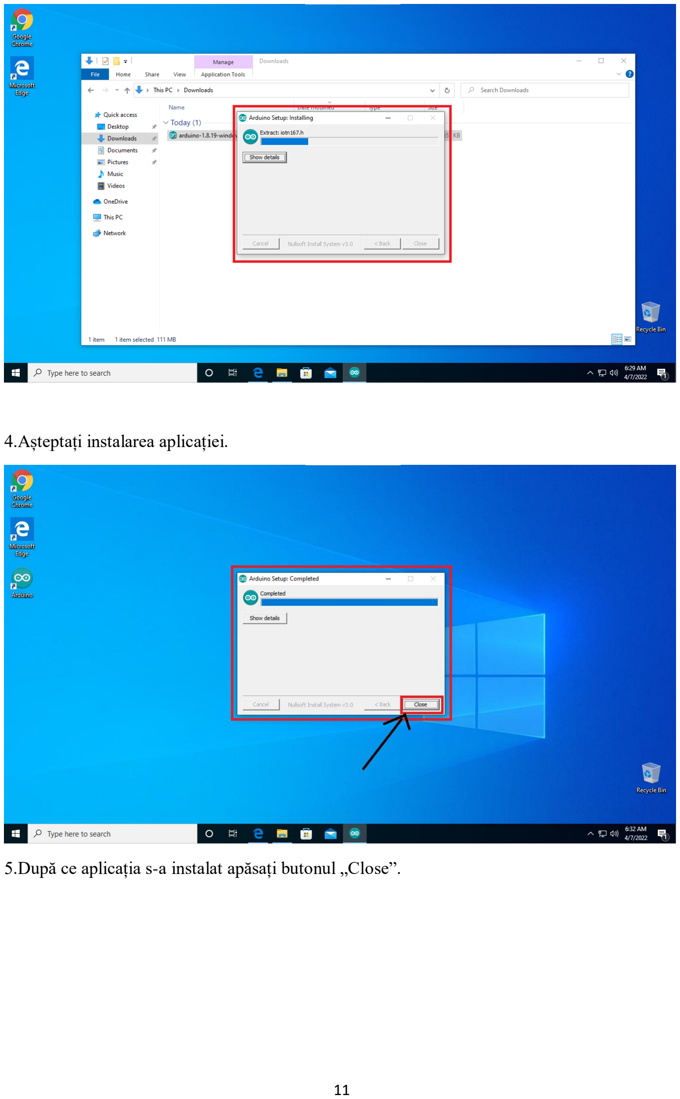
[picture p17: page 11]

4.Așteptați instalarea aplicației.

5.După ce aplicația s-a instalat apăsați butonul „Close”.

Deschiderea mediului de programare va arăta ca în imaginea de mai jos:

În cazul în care nu ați mai folosit Arduino se va deschide o filă goală asemănătoare cu cea din imaginea de mai sus.

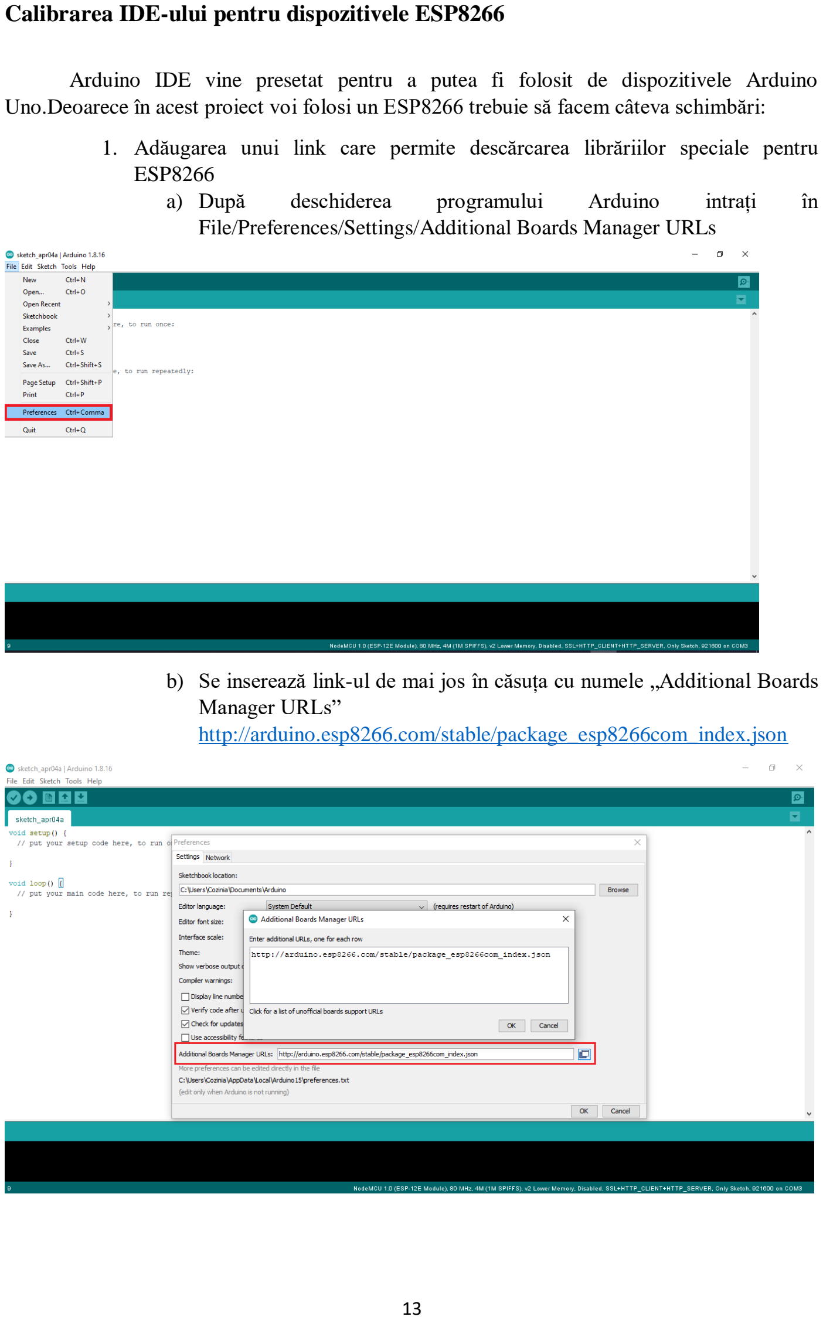
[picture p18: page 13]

Calibrarea IDE-ului pentru dispozitivele ESP8266

Arduino IDE vine presetat pentru a putea fi folosit de dispozitivele Arduino Uno.Deoarece în acest proiect voi folosi un ESP8266 trebuie să facem câteva schimbări:

1. Adăugarea unui link care permite descărcarea librăriilor speciale pentru ESP8266
a) După | deschiderea | programului | Arduino | intrați | în
File/Preferences/Settings/Additional Boards Manager URLs
b) Se inserează link-ul de mai jos în căsuța cu numele „Additional Boards Manager URLs”
http://arduino.esp8266.com/stable/package_esp8266com_index.json

2.Instalarea librăriei ESP8266

a) Se deschide meniul Tools/Boards/Board Manager
b) În fereastra deschisă se caută „esp8266 by ESP8266 Community” și se instalează versiunea 2.4.1(aceasta este versiunea folosită în acest proiect)

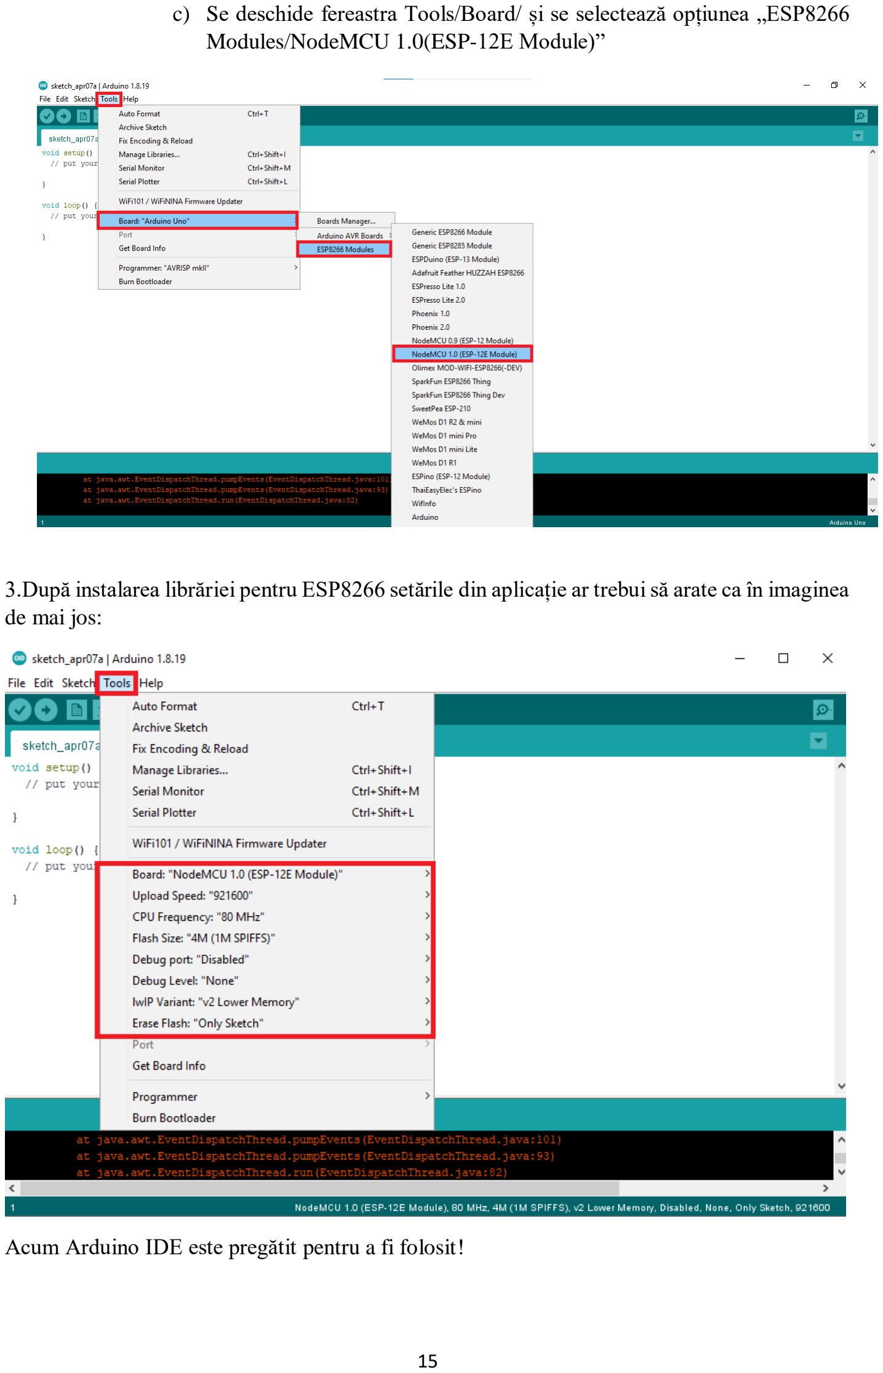
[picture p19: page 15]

c) Se deschide fereastra Tools/Board/ și se selectează opțiunea „ESP8266 Modules/NodeMCU 1.0(ESP-12E Module)”

3.După instalarea librăriei pentru ESP8266 setările din aplicație ar trebui să arate ca în imaginea de mai jos:

Acum Arduino IDE este pregătit pentru a fi folosit!

## Noțiuni de bază despre NodeMCU ESP8266

Aceste plăcuțe sunt de diferite feluri însă în acest proiect se folosește un ESP8266(versiunea 12E), așadar mai jos sunt descrise câte lucruri esențiale despre acest tip de plăcuțe.

Mai jos este inserată o poză ce reprezintă configurația pinilor unui ESP8266.

Placa de dezvoltare NodeMCU ESP8266 vine cu modulul ESP-12E care conține cipul ESP8266 având microprocesor Tensilica Xtensa pe 32 de biți LX106 RISC. Acest microprocesor acceptă RTOS și funcționează la o frecvență reglabilă de la 80 MHz la 160 MHz. NodeMCU are 128 KB RAM și 4 MB de memorie Flash pentru a stoca date și programe. Puterea sa mare de procesare cu Wi-Fi sau Bluetooth încorporat și funcțiile de operare în stand-by îl fac ideal pentru proiecte IoT.

Aceste dispozitive au o memorie totală de 32MB(doar 4 MB sunt disponibili pentru a scrie programe), 11 pini digitali(D0-D10), un pin Analog(A0), 3 pini ce pot oferi curent de 3.3V, un pin ce oferă 5V, 4 pini de ground.Aceste microprocesoare suportă I2C(magistrală de comunicații seriale) pe pinii D1(clock) și D2(Data) și suport de extindere a memoriei printr-un modul de SD card ce folosește pinii MISO, MOSI, SCK, SS.

Pinii I2C sunt folosiți pentru a conecta senzori și periferice I2C. Sunt acceptate atât I2C Master, cât și I2C Slave. Funcționalitatea interfeței I2C poate fi realizată programatic, iar frecvența este de maximum 100 kHz. Trebuie remarcat faptul că frecvența I2C ar trebui să fie mai mare decât frecvența cea mai lentă a dispozitivului slave.

## Noțiuni de bază în Vue.js

Date introductive despre Vue.js

Povestea Vue.js începe în 2013, când Evan You lucra la Google, creând o mulțime de prototipuri chiar în browser. În acest scop, Evan a folosit practici din alte framework-uri cu care a lucrat și a lansat Vue.js în mod oficial în 2014. De atunci, acesta evoluează continuu. La începutul lui 2018, Vue.js a început să bată Angular și să devină mai faimos pe piață. Mai târziu, în septembrie 2018, Evan You a decis să anunțe lansarea Vue 3.0. Vue.js evoluează continuu odată cu creșterea rapidă a utilizării și a comunității acestui framework. Comunitatea va continua să crească, deoarece a fost construită pe cea mai bună combinație de caracteristici Angular și React.

Într-un interviu, Evan dezvăluie că inițial Vue.js a fost o încercare de a lua ce e mai bun din Angular și de a construi un instrument personalizat, dar mai ușor: "Pentru mine, Angular oferea ceva grozav, și anume data binding și un mod de a trata un DOM bazat pe date, astfel încât să nu fie nevoie să atingi tu însuți DOM-ul."

Vue.js este un framework progresiv pentru JavaScript folosit pentru a construi interfețe web și aplicații de o pagină. Vue.js nu este folosit doar pentru interfețe web, ci și pentru dezvoltarea de aplicații desktop și mobile cu ajutorul framework-ului Electron. Extensia HTML și baza JS au făcut rapid din Vue un instrument front-end favorit, dovadă fiind adoptarea de către giganți precum Adobe, Behance, Alibaba, Gitlab și Xiaomi.

Vue.js este un framework JavaScript progresiv, care este folosit pentru a construi interfețe UI (interfețe ușor de folosit de către utilizatori) și SPA (aplicații cu o singură pagină). Acest framework este renumit pentru curba sa de învățare rapidă. Este o bibliotecă atât de ușor de învățat și accesibilă, încât, putem începe să construim aplicații web în Vue.js folosind cunoștințele de HTML, CSS și JavaScript. Curba de învățare rapidă este un fel de semnătură a acestui framework.

Construirea unui program simplu care folosește Vue.js 3

Deoarece în cadrul acestui proiect este folosită versiunea a treia a framework-uliu Vue.js, mai jos este prezentată o mică aplicație care folosește această versiune de Vue.

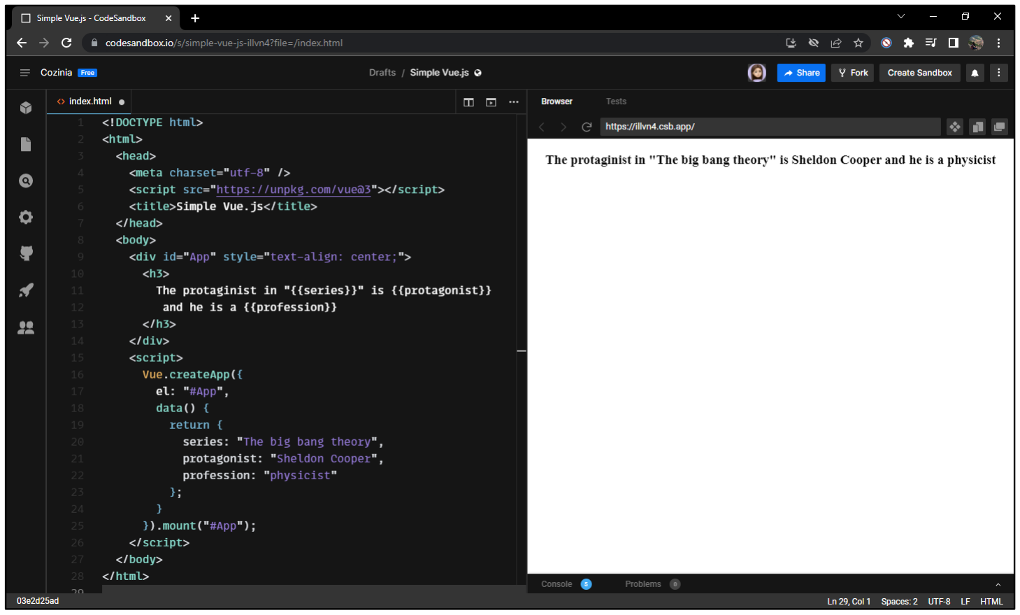
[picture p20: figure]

Așa cum se poate vedea în imaginea de mai sus s-a construit un program foarte simplu în Vue.js.În următoarele rânduri este enunțată procedura de creare:

1) Construirea un fișier HTML simplu.
2) Pentru a folosi Vue.js se inserează în header următoarea linie de cod:
<script src="https://unpkg.com/vue@3"></script>

P.S:Aceasta se numește CDN și ne ajută să folosim vue.js în aplicația noastră HTML fără a fi nevoiți să instalăm framework-ul.

3) Se adaugă un <div> cu id-ul „App”.
4) În body se deschide un script.
a) În script se adaugă aplicația „Vue.createApp” în cadrul căreia se construiesc componentele Vue.js.
b) În „data()” se introduc valorile „series”, „protagonist”și „profession” cărora li se atribuie câte un string cu diferite informații.
5) Pentru ca aplicația Vue.js să funcționeze este importană adăugarea sintaxei „.mount(„#App”)”.Această instrucțiune „împachetează totul”.
P.S.:Aplicația web de mai sus poate fi vizualizată la adresa:

https://codesandbox.io/s/simple-vue-js-illvn4?file=/index.html:64-112

## Descrierea componentelor folosite

În cadrul acestui proiect voi fi folosite mai multe componente așa că mai jos se află o mică prezentare a acestora și cum sunt legate la microcontroler.

Numărătorul de monede
Primul pe ordinea de idei este numărătorul de monede, CH-926 pe numele de cod, acesta acceptă până la 3 tipuri diferite de monede.

Acest modul trebuie conectat la o sursă de 12V , iar pinul ce se ocupă cu transmiterea mesajului de identificare a monedelor trebuie conectat la unul dintre pinii digitali ai microcontroler-ului ca în schema de mai jos.

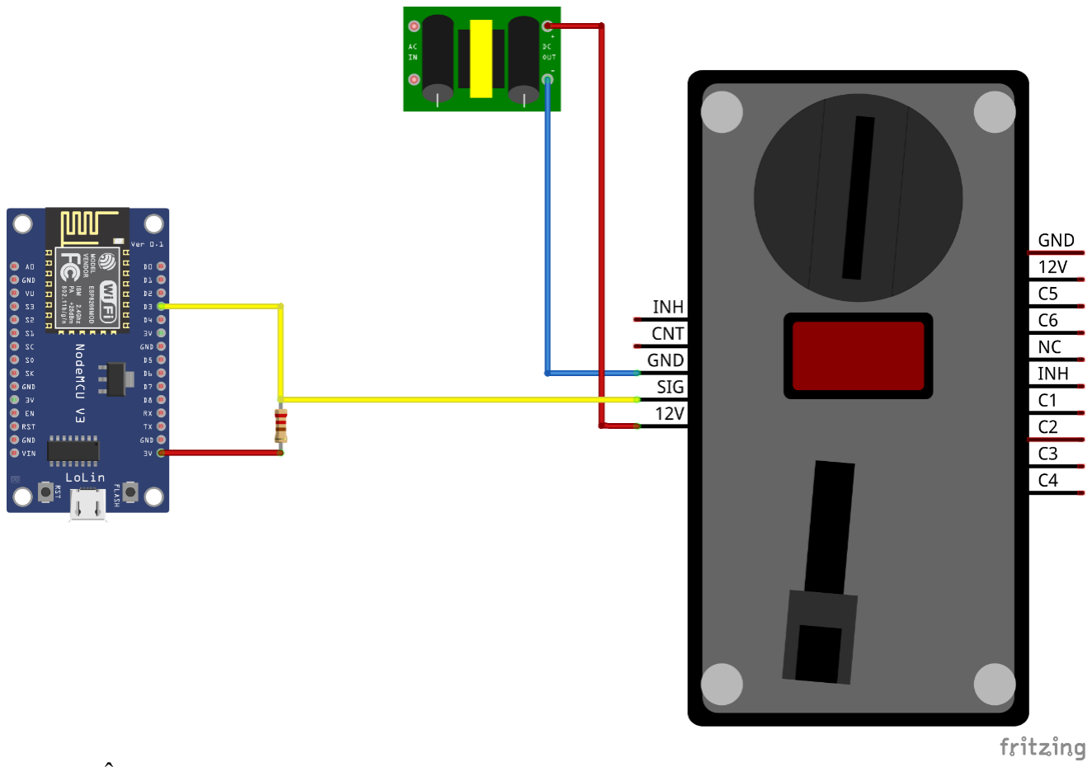
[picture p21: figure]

În desen se observă microcontroler-ul în partea stângă, sursa de 12V în partea de sus și numărătorul de monede în partea dreaptă.Acesta este conectat la sursa externă de 12V prin cele două fire(roșu pentru VCC și albastru pentru GND), iar prin firul de culoare galbenă la ESP8266, mai exact la 3V3 ce unește printr-un tranzistor pinul SIG(Coin) al acceptorului de monede cu pinul digital D3 al plăcuței.

Modulul este progrmat pentru a distinge 3 monede diferite(de 5, 10 și 50 bani).Acesta se bazează pe pulsuri consecutive pentru fiecare tip de monedă în parte(un puls pentru 5 bani, două pulsuri pentru 10 bani, trei pulsuri pentru 50 de bani).

Iată câteva secvențe de cod interesante:

Pentru a nu supraîncărca plăcuța cu citiri successive se folosește attachInterrupt, metodă cu ajutorul căreia funcția CoinEvent este invocată doar la detectarea introducerii unei monede.

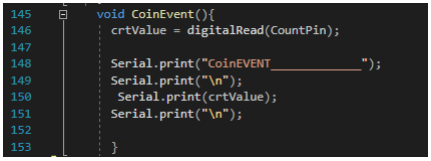
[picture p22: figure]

digitalRead citește valoarea pinului Count și o stochează în variabila crtValue.

Funcția Coins se apelează în loop.Dacă timpul curent este diferit de cel anterior iar valoarea curentă de cea anterioară, timpul anterior ia valoarea celui prezent și valoarea anterioară ia valoarea celei prezente.Variabila de tip bool numită changed își schimbă valoarea în true când această condiție este îndeplinită.Dacă diferența dintre timpul curent și cel anterior este mai mare de 30 de milisecunde, iar changed este true, variabila number crește cu o unitate.

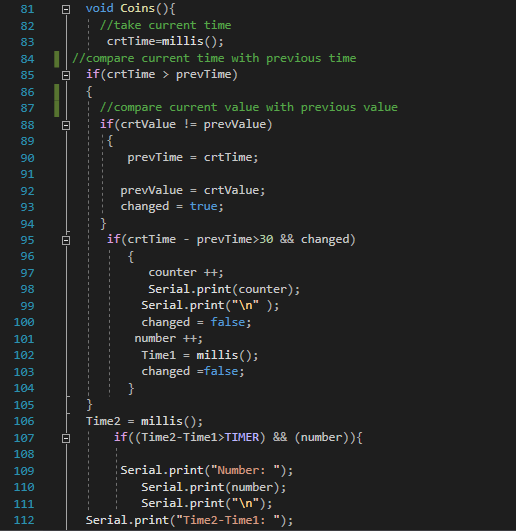
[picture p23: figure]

În funcție de valoarea variabilei number, aceasta îndeplinește una dintre condițiile de mai sus.În acest fel creditul crește cu o anumită valoare(5, 10 sau 50 de bani), valoarea number este resetată la 0, iar variabila totalCoins crește cu o unitate pentru a înregistra numărul total de monede de un anumit tip.

Display-ul
După punerea în funcțiune a numărătorului de monede a fost adăugat și un display pe care să afișeze creditul inserat.Mai jos este inserată o schemă ce conține și display-ul.

Display-ul comunică prin protocolul I2C cu microcontroler-ul.Pentru a face acest lucru posibil se conectează pinii D1 la SCL(reprezentat prin cablul de culoare mov), D2 la SDA(reprezentat prin cablul de culoare oranj), pinul VIN(cel care transportă curent de 5V) la VCC și GND la GND.

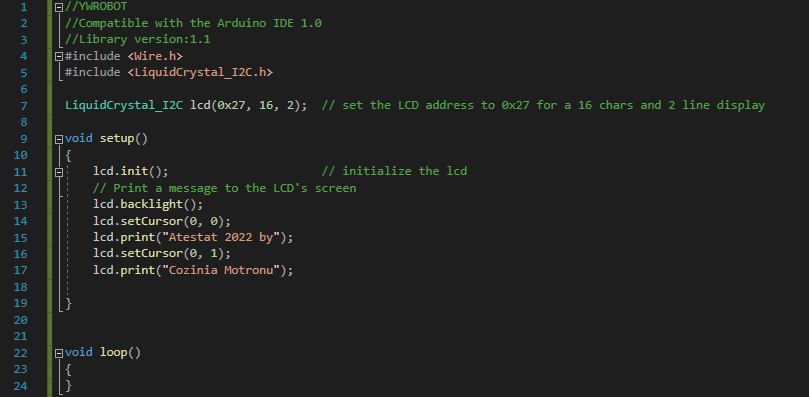
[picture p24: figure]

Acest cod folosește librăria „LiquidCrystal_I2C”.După declararea directivelor preprocesor „Wire” și „LiquidCrystal_I2C” se inițializează obiectul lcd care se află la adresa 0x27.În funcția setup se inițializează lcd, backlight și se setează cursorul pe poziția linia 0 și coloana 0 pentru a scrie un mesaj, respectiv lini 1 și coloana 0 pentru continuarea mesajului.

Mai jos este inserată o poză cu un mesaj afișat pe display.

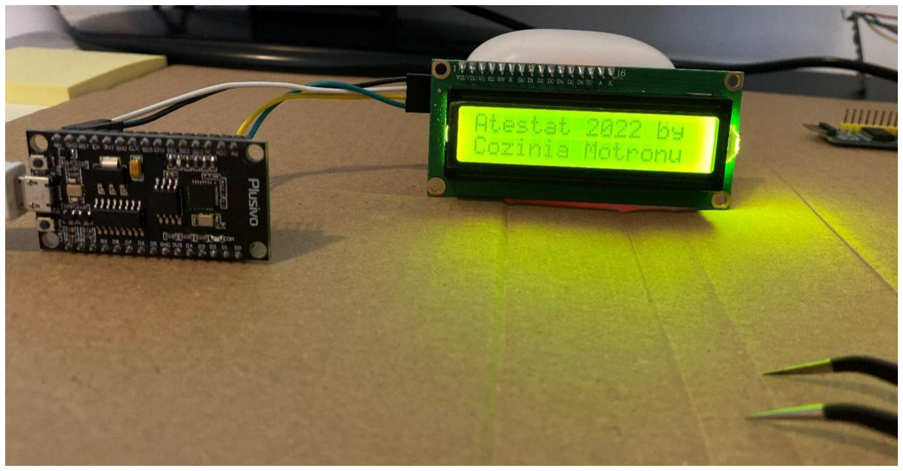
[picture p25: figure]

Motoarele

Acum schema începe să se încarce deoarece fiecare motor are 4 fire cu ajutorul cărora se conectează la shield-ul CNC și alte două care duc la modulul de expansiune PCF8574.Se folosesc aceste module deoarece atât motoarele, cât și celelalte componente ocupă foarte mulți pini și nu lasă loc disponibil pe microcontroler. PCF8574 folosește același protocol precum display-ul, adică I2C pentru a transmite diferite evenimente ce se petrec pe pini.Acest lucru este convenabil deoarece se pot lega mai multe module de expansiune pentru a extinde numărul de pini.Aceste module se diferențiază prin adresă, fiecare putând fi programat manual ca având o anumită adresă(de la 0x20 la 0x27) așa cum este ilustrat în imaginea de mai jos.

Shield-ul CNC împreună cu driver-ul de motoare A4988 asigură buna funcționare a motoarelor oferind o interfață ușor de utilizat.

Shield-ul oferă suport pentru maxim 4 drivere de motoare, un pin Enable(EN) pentru a activa mișcarea motoarelor, mai mulți pini de ground(GND),pini care permit mișcarea motoarelor într-o anumită direcție și un anumit număr de pași, de exemplu: X.STEP(indică numărul de pași pe care motorul X să îl parcurgă), X.DIR(direcția în acre să se învârtă motorul X).Shield-ul trebuie alimentat cu 12V de la o sursă externă și 5V(curent necesar cerut de driver-ele de motoare).

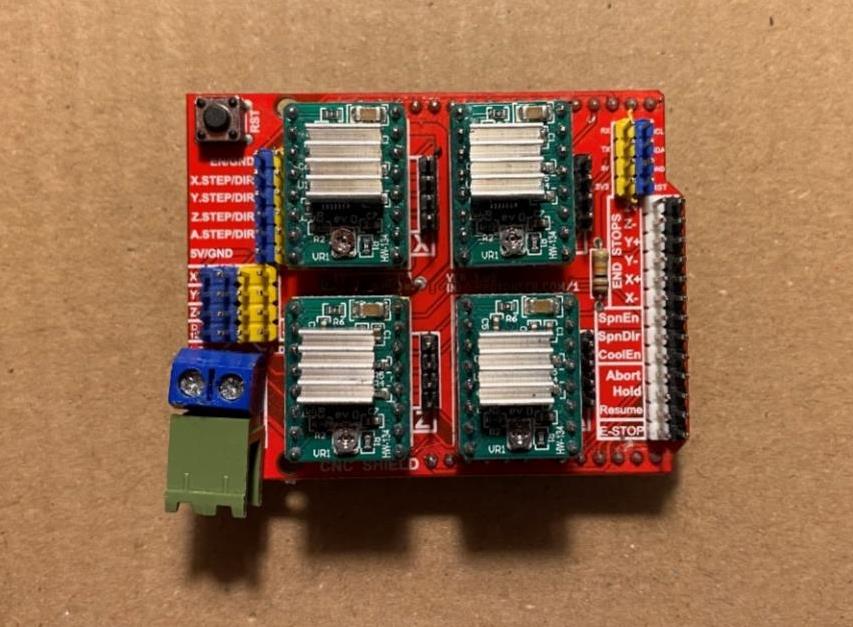
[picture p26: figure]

Mai jos se poate observa schema proiectului la care se adaugăt motoarele, shield-ul cu driver-ele de motoare și modulele de expansiune a pinilor.

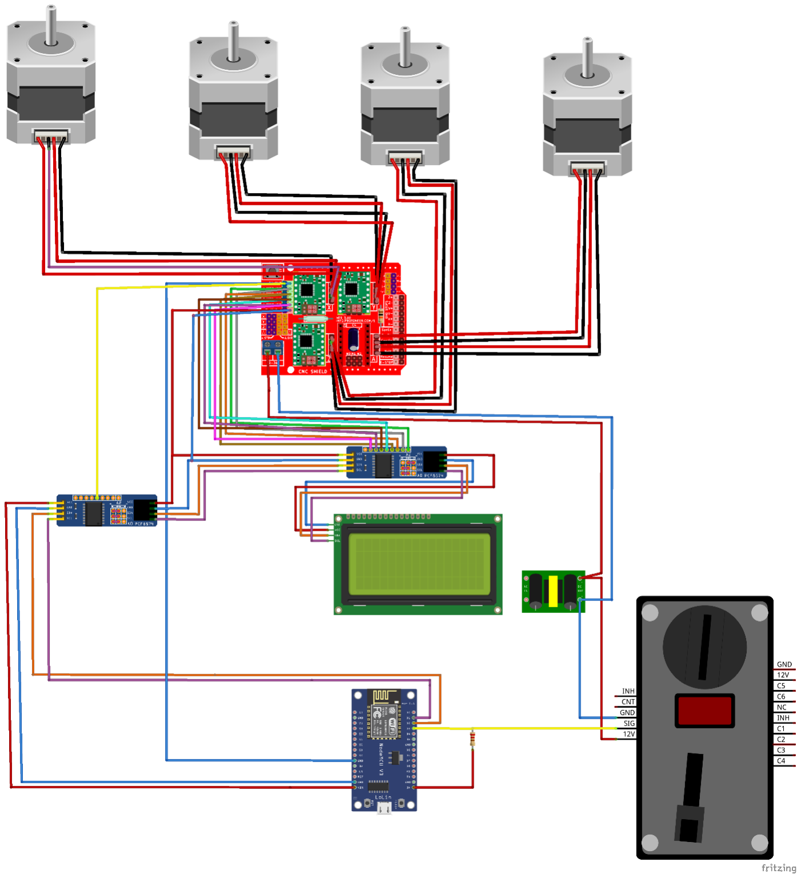
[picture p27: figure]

Modulul RFID

RFID este acronimul de la "radio-frequency identification" (identificare prin radiofrecvență) și se referă la o tehnologie prin care datele digitale codificate în etichete RFID sau etichete inteligente sunt captate de un cititor prin intermediul undelor radio.Tehnologia RFID este similară codului de bare, în sensul că datele de pe o etichetă sunt capturate de un dispozitiv care stochează datele într-o bază de date. Cu toate acestea, RFID are mai multe avantaje față de sistemele care utilizează un software de urmărire a activelor cu coduri de bare. Cel mai notabil este faptul că datele din etichetele RFID pot fi citite în afara liniei de vizibilitate, în timp ce codurile de bare trebuie aliniate cu un scaner optic.

Modul de utilizare este destul de simplu: utilizatorul apropie cardul de scanner și datele sunt citite și prelucrate.În cazul acestui proiect utilizatorul folosește cardul pentru a se înregistra la vendomat, nemaifiind nevoie să introducă bani pentru a achiziționa produse.

Modulul RFID este conectat ca în schema de mai jos la pinii următori:

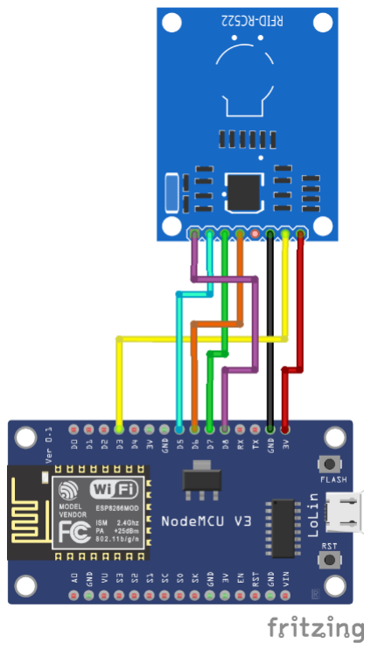
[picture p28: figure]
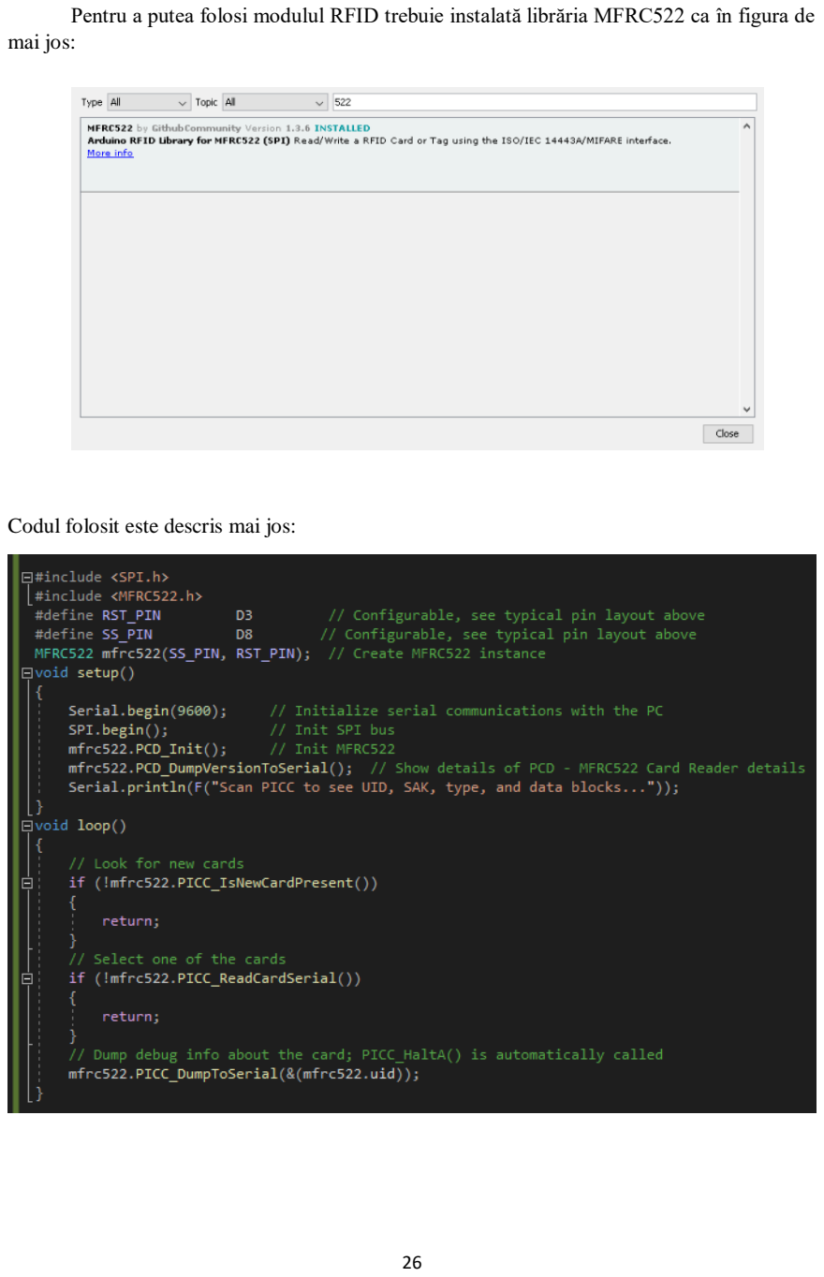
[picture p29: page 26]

Pentru a putea folosi modulul RFID trebuie instalată librăria MFRC522 ca în figura de mai jos:

Codul folosit este descris mai jos:

După încărcarea acestui cod pe serială ar trebui să apară un mesaj asemănător cu cel de mai jos(mesajul poate să difere în funcție de versiunea moduluului RFID) unde puteți scana cardul.

Mai departe în implementarea codului care va identifica ID-ul cardului se va folosi „Card UID” .

## Stocarea datelor

Din cauza limitărilor spațiului de stocare pe care le au microcontroler-ele ESP8266(8MB RAM), nu este posibilă realizarea unei baze de date care să stocheze utilizatorii, produsele și tranzacțiile și în același timp să execute și comenzile celorlalte componente.În acest caz se folosesc structuri care imită tabelele enumerate mai sus.Acestea sunt realizate într-o clasă numită FileDb.

Această structură reține CNP-ul, nume, prenumele, parola, numărul cardului RFID, creditul, statutul utilizatorului(dacă este sau nu administrator) , iar parametrul Enabled are valoarea 1 dacă acesta este activ și 0 în caz contrar.Celelalte structuri arată similar.

După cum îi spune și numele, funcția „AddUser()” adaugă utilizatori.Aceasta primește ca parametru o entitate de tip User* și verifică dacă CNP-ul utilizatorului care se dorește să fie introdus se află deja în structură.Dacă da, funcția returnează 1, iar în caz contrar stochează datele noului utilizator și crește userCount.Procesul este similar pentru produse și tranzacții.

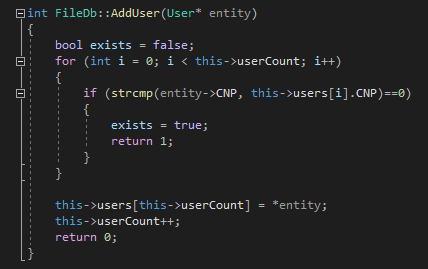
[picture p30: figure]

În funcția „InitData” sunt creeați câțiva utilizatori, produse și tanzacții urmând modelul din figurile inserate mai jos.

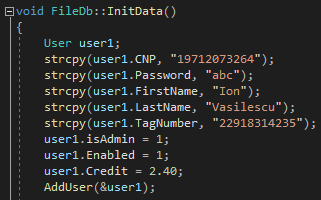
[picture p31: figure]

## Aplicația web

Aplicația web este construită folosind HTML, CSS și VueJS.Din cauza spațiului mic de stocare al microcontroler-ului această aplicație web este construită pe o singură pagină.

Primul element care va apărea în pagină este formularul de logare.În acest formular utilizatorul va introduce CNP-ul și parola.Prin apăsare butonului „Login” se va apela funcția „LogIn()”.

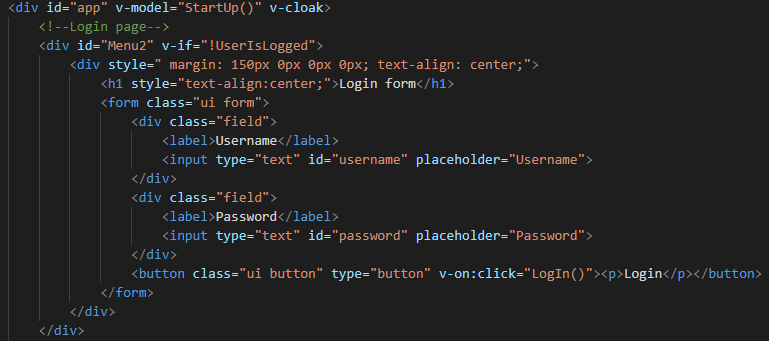
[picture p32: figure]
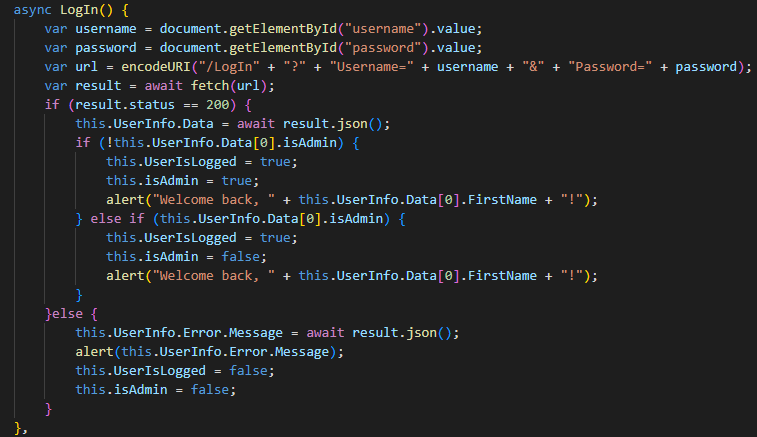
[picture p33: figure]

Această funcție este de tip async deoarece așteaptă rezultatul de la server.Datele introduse de utilizator sunt aduse aici prin instrucțiunea „document.getElementById”.Acestea sunt trimise la server și interpretate.

Această funcție se află pe server și interpretează datele introduse.Acestea sunt preluate din aplicația web prin instrucțiunea „server.arg(„ExNume”)”.Variabila user de tip User* stochează răspunsul funcției „GetElementByCNP” aflată în clasa FileDb.

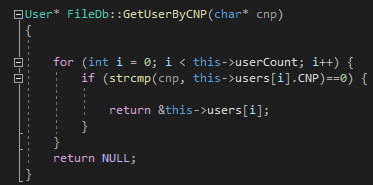
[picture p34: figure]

Această funcție verifică dacă parametrul cnp corespunde utilizatorului users[i].În caz afirmativ returnează datele utilizatorului, iar în caz contrar NULL.

În funcția „LogIn” se verifică dacă parola utilizatului primit anterior corespunde cu cea trimisă din aplicația web.În caz afirmativ datele se formatează în format json folosind funcția sprintf și se trimit în pagina web ca răspuns alături de codul 200(ok).În caz contrar se trimite codul de eroare 601(acest cod este creat de mine și înseamnă „CNP sau parolă invalidă”).În cazul în care nici parola și nici CNP-ul nu se potrivesc cu datele existente deja se trimite codul de eroare 602(utilizatorul nu există).

Dacă CNP-ul și parola se potrivesc, pe client se primește codul 200(ok) și se verifică dacă utilizatorul este administrator sau nu.În acest afirmativ, variabila de tip bolean isAdmin ia valoarea true, în caz contrar ia valoarea false.În ambele dintre aceste cazuri este afișat mesajul „Welcome back” urmat de numele utilizatorului.În caz că datele introduse nu se potrivesc celor existente în structură se ba afișa mesajul venit de la server stocat în UserInfo.Error.Message.

După ce utilizatorul a fost logat variabila de tip bolean UserIsLogged ia valoarea true, iar în funcție de valoarea variabilei isAdmin se afișează meniul administratorului sau al utilizatorului.

Meniul administratorului
Mai jos este inserată o captură de ecran reprezentând structura paginii administratorului.Acesta poate vedea lista utilizatorilor și a produselor, poate adăuga utilizatori și produse, poate deschide ușa vendomatului și nu în ultimul rând, poate testa funcționalitatea motoarelor.

Meniul de vizualizare a utilizatorilor afișează toți utilizatorii și informațiile acestora.În acest meniu administratorul poate edita datele acestora și îi poate dezactiva.

Pentru a face acest lucru posibil, la apăsarea butonului „ViewUsers” se apelează funcția „GetUsers”.

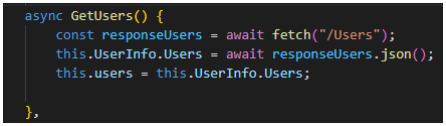
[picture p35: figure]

Această funcție se conectează la funcția Users din server și preia datele tuturor utilizatorilor existenți precum este prezentat în imaginea de mai jos.

Informațiile utilizatorilor sunt formatate în format json în funcția snprintf în variabila de tip char TempBuffer.După care se pune o virgulă între datele utilizatorilor și se concatenează în variabila de tip char MyBuffer folosind funcția strcat.La final se trimite variabila MyBuffer în aplicația web și codul 200. Acestea sunt afișate pe ecran într-un tabel.

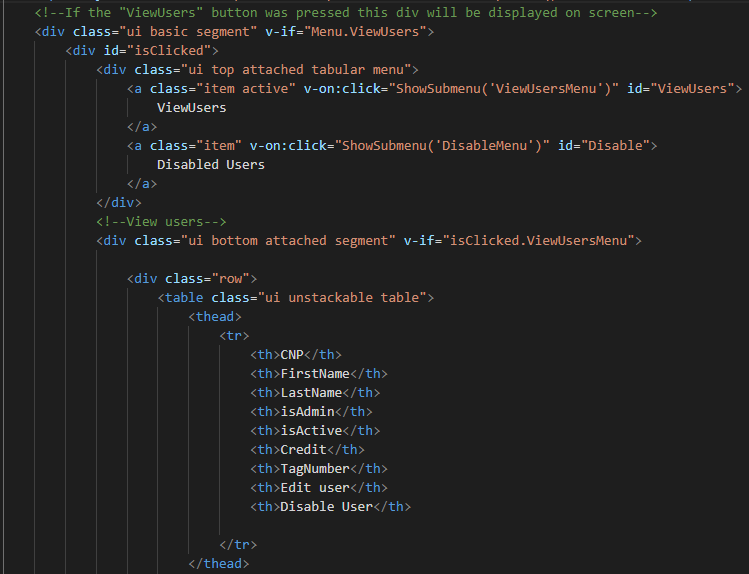
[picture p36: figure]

Apăsând iconița de edit se va deschide modal-ul de mai jos în care se pot edita informațiile utilizatorului.

Prin apăsarea butonului aceste informații ajung în funcția „EditUser” de unde sunt trimise pe server unde sunt prelucrate.Dacă prelucrarea s-a putut face atunci serverul va returna codul 200, în caz contrar va returna un cod de eroare.

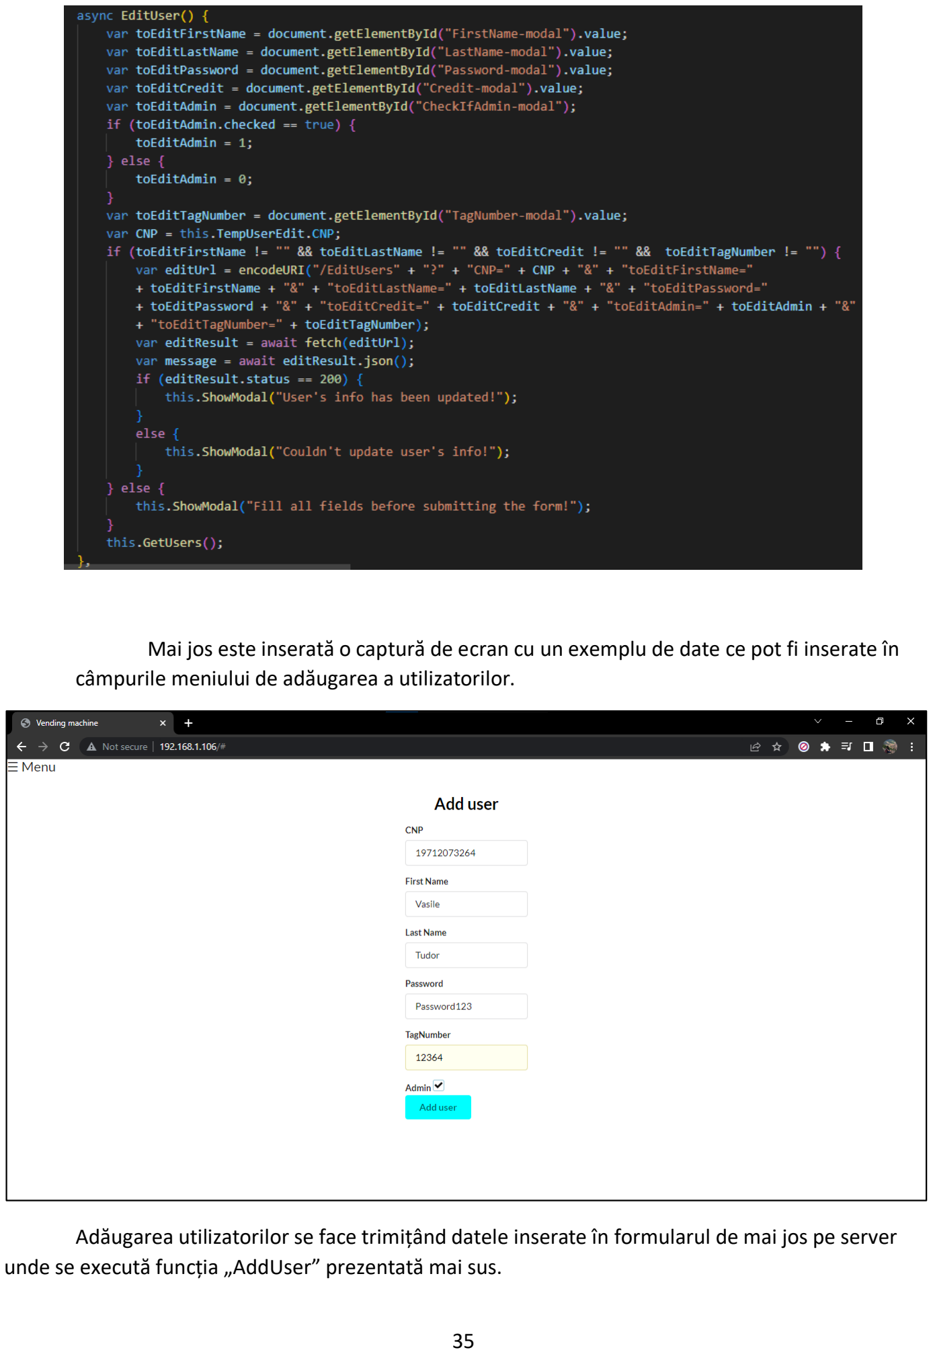
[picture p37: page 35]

Mai jos este inserată o captură de ecran cu un exemplu de date ce pot fi inserate în câmpurile meniului de adăugarea a utilizatorilor.

Adăugarea utilizatorilor se face trimițând datele inserate în formularul de mai jos pe server unde se execută funcția „AddUser” prezentată mai sus.

## Modul de funcționare al vendomatului

Modul de funcționare de bază:

Clientul introduce monede în vendomat, selectează produsul dorit, iar vendomatul returnează produsul.

Cum funcționează procesul de selecție:

- Butonul a fost apăsat
- Se verifică stocul produsului
- Se verifică dacă creditul inserat de utilizator este suficient pentru produsul selectat
- În cazul în care toate condițiile au fost îndeplinite vendomatul returnează produsul clientului

Vendomatul suportă 3 tipuri de monede(5, 10 și 50 de bani), 4 tipuri de produse din care utilizatorul poate alege și două moduri: standard și company.

În modul standard clientul inserează monede în vendomat, vede creditul introdus pe ecran, selectează produsul dorit , iar vendomatul îl returnează.

Pentru a vedea aplicația web din modul company este necesară conectarea la aceeași rețea ca cea a vendomatului.

În modul company utilizatorul scanează cardul RFID pentru a se autentifica, selectează produsul dorit , iar vendomatul îl returnează.În acest mod de funcționare utilizatorul are un cont la care se poate loga și unde poate vedea tranzacțiile făcute și creditul rămas.

Modul de funcționare a sistemului de logare cu cardul RFID:

- Utilizatorul scanează cardul
- Un mesaj este afișat pe ecran
- După 3 secunde pe ecran este afișat creditul
- Începe procesul de selecție prezentat mai sus
- După terminarea procesului de selecție clientul apasă buton de logout

Modul company vine și cu un cont de administrator unde acesta poate vedea, edita sau adăuga utilizatori și produse și nu în ultimul rând, poate testa funcționalitatea motoarelor.

## Bibliografie

Surse folosite în această lucrare:

- Informații despre C++:

Sursă 1: https://www.toptal.com/c/the-ultimate-list-of-resources-to-learn-c-and-c-plus-plus

Sursă 2: https://www.techopedia.com/definition/26184/c-plus-plus-programming-language

- Despre C++

Sursă: caietul de informatică de clasa a X-a

- Limbajul Arduino:

Sursă 1: https://flaviocopes.com/arduino-programming-language/

Sursă 2: https://www.arduino.cc/en/Guide/Introduction

Sursă 3: https://en.wikipedia.org/wiki/Arduino

- Noțiuni de bază despre NodeMCU ESP8266
Sursă | 1: | https://components101.com/development-boards/nodemcu-esp8266-pinout-features-and-
datasheet (https://components101.com/development-boards/nodemcu-esp8266-pinout-features-and-datasheet)

Sursă 2: https://www.make-it.ca/nodemcu-details-specifications/

| | • Poză ESP8266

Sursă: https://diyi0t.com/wp-content/uploads/2019/06/NodeMCU_pinout.png

| | • Informații generale Vue.js

Sursă 1: https://linuxhint.com/about_vue_js/

Sursă 2: https://www.altexsoft.com/blog/engineering/pros-and-cons-of-vue-js/

| | • Poză adrese PCF8574

Sursă: https://www.instructables.com/PCF8574-GPIO-Extender-With-Arduino-and-NodeMCU/

| | • Poză conectarea pinilor modulului RFID la ESP8266:

Sursă: http://www.esp8266learning.com/esp8266-rfid-rc522-module-example.php

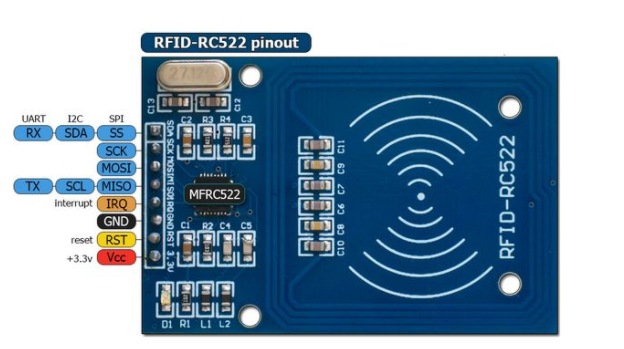
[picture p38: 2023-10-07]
Arduino/MyProjects/RFID/RFIDPinout.png

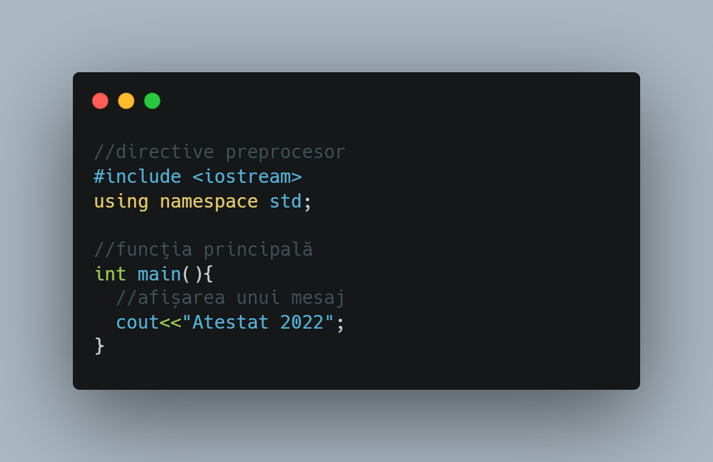
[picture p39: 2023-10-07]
src/C++/Program C++.png

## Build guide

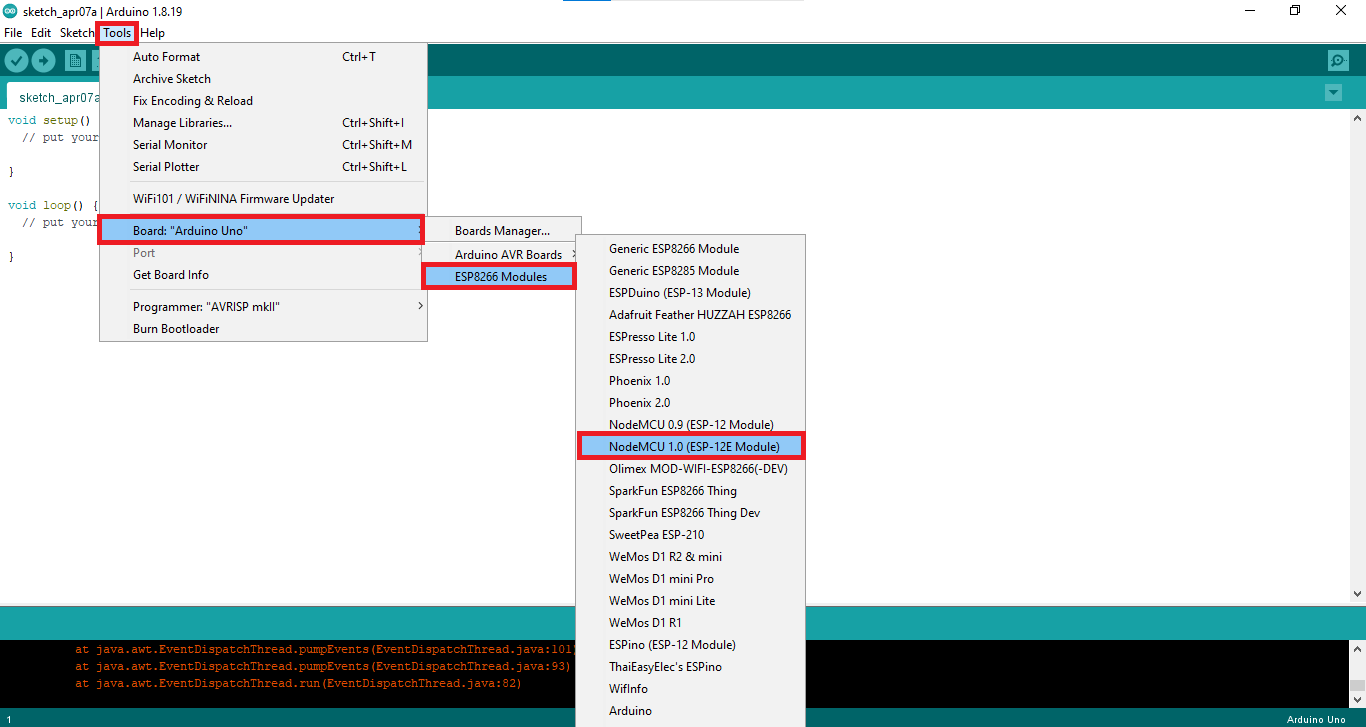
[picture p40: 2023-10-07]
src/Arduino IDE/InstallingESP8266BoardLibraries2.png

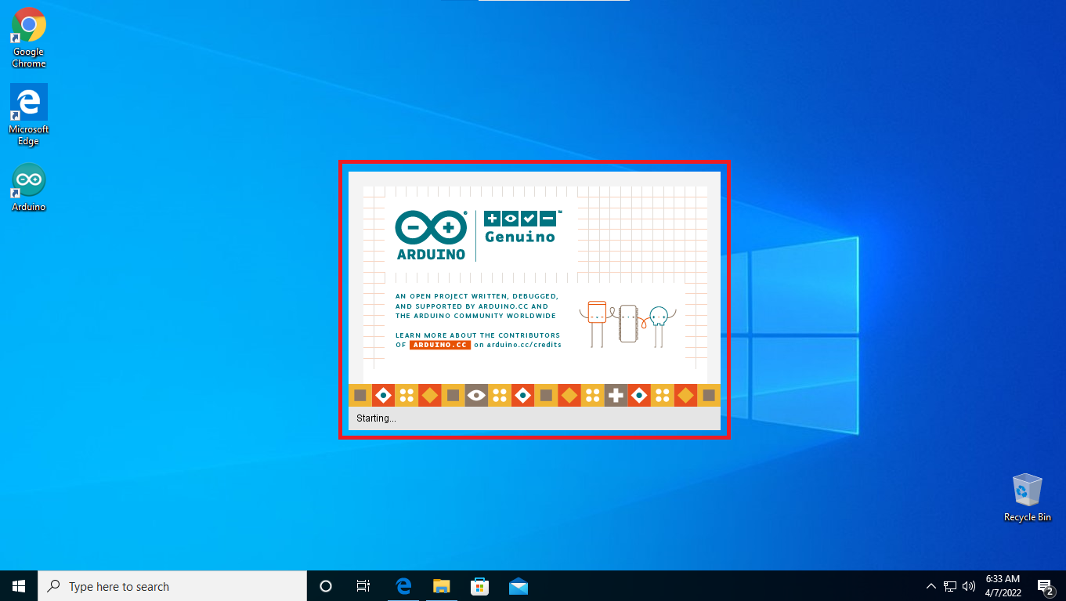
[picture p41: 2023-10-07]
src/Arduino IDE/InstallArduino_Step6.png

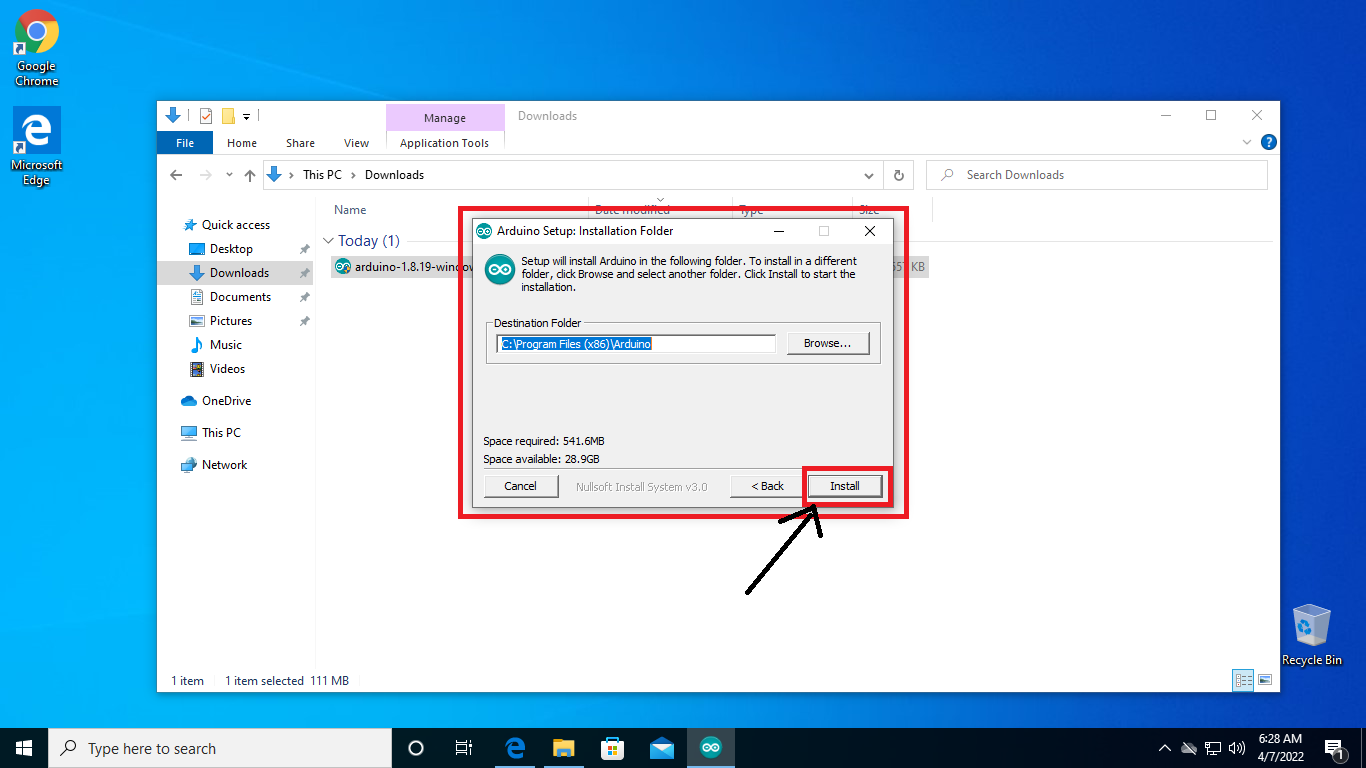
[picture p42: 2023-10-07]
src/Arduino IDE/InstallArduino_Step3.png

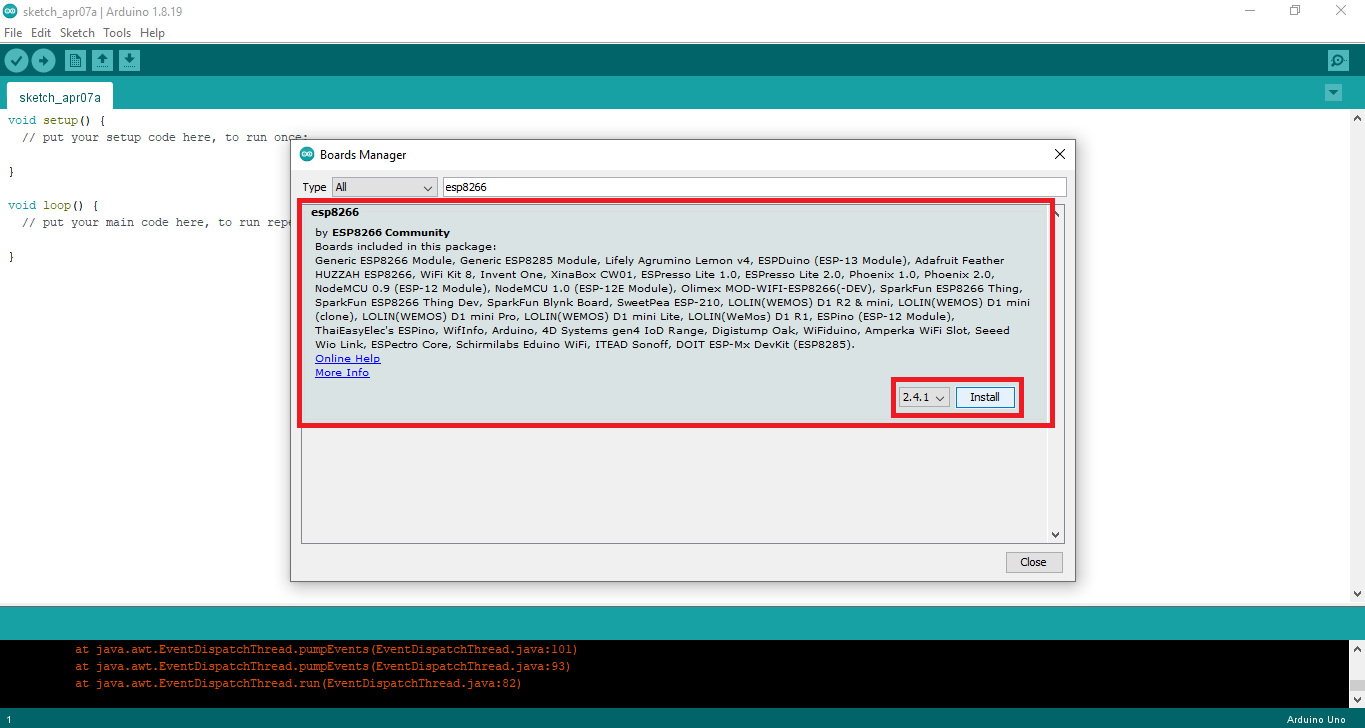
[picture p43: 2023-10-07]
src/Arduino IDE/InstallingESP8266BoardLibraries1.png

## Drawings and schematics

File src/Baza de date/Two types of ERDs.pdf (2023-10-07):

## First scenario:multiple ERDs related with Action's entity

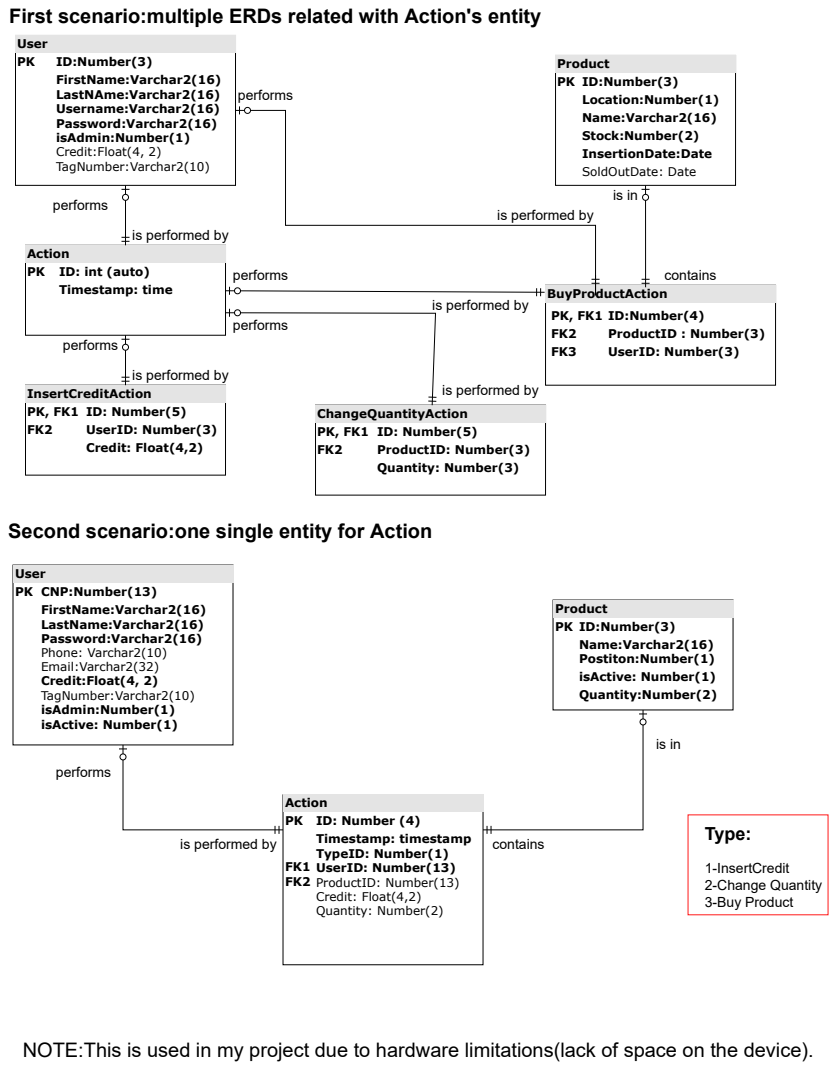
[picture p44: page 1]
User; ID:Number(3); FirstName:Varchar2(16) LastNAme:Varchar2(16) Username:Varchar2(16) Password:Varchar2(16) isAdmin:Number(1) Credit:Float(4, 2) TagNumber:Varchar2(10); Timestamp: time; BuyProductAction; ProductID : Number(3); UserID: Number(3); Credit: Float(4,2); ProductID: Number(3); Quantity: Number(3)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

Product
PK ID:Number(3)
Location:Number(1)
Name:Varchar2(16)
Stock:Number(2)
InsertionDate:Date
SoldOutDate: Date

is performed by

Action
PK ID: int (auto)

PK, FK1 ID:Number(4)

InsertCreditAction
PK, FK1 ID: Number(5)

ChangeQuantityAction

Second scenario:one single entity for Action

Postiton:Number(1)
isActive: Number(1)
Quantity:Number(2)

PK ID: Number (4)
Timestamp: timestamp
TypeID: Number(1)
UserID: Number(13)
ProductID: Number(13)
Credit: Float(4,2)
Quantity: Number(2)

NOTE:This is used in my project due to hardware limitations(lack of space on the device).

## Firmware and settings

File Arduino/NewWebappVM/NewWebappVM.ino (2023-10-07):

/*
//Users
const char* const createTableUser = "CREATE TABLE Users (CNP INTEGER PRIMARY KEY, FirstName VARCHAR2(16), LastName VARCHAR2(16), Password VARCHAR2(12) NOT NULL, TagNumber VARCHAR2(16), Credit NUMBER(4,2) NOT NULL, IsAdmin NUMBER(1) NOT NULL, IsActive NUMBER(1) NOT NULL);";
//const char* const createTableUser = "CREATE TABLE Users(id integer PRIMARY KEY, FirstName text not null, LastName text not null, Username text not null, Password text not null, IsAdmin integer not null,Credit float(4,2), TagNumber text);";
const char* const insertUser = "INSERT INTO Users (CNP, FirstName, LastName, Password, Credit, isAdmin, isActive) VALUES (19712073264,'Ion', 'Vasilescu', 'abc', 4.85, 1, 1);";
//const char* const insertUser = "INSERT INTO Users (FirstName, LastName, Username, Password, IsAdmin, Credit, TagNumber) VALUES ('Ion', 'Vasilescu', 'ion.vasilescu', 'abc', 0, 8.40, '#165652JJFV');";

const char* insertUser2 = "INSERT INTO Users (CNP, FirstName, LastName, Password, Credit, isAdmin, isActive) VALUES  (1, 'Anonymus', 'Anonymus', '1', 0, 0, 1 );";

//Products
const char* const createTableProducts = "CREATE TABLE Product (ID INTEGER PRIMARY KEY, Name VARCHAR2(30),Price NUMBER(2,1), Position NUMBER(1), isActive NUMBER(1) NOT NULL, Quantity NUMBER(2) NOT NULL);";
//const char* const createTableProducts = "CREATE TABLE Products(id integer PRIMARY KEY,Location integer not null, Name text not null,Stock integer not null, InserationDate date not null, SoldOutDate date);";
//Actions
const char* const createTableTransactions = "CREATE TABLE Transaction(ID INTEGER PRIMARY KEY, Timestamp TIMESTAMP NOT NULL, TypeID NUMBER(1) NOT NULL, Credit NUMBER(4,2), Quantity NUMBER(2));";
//const char* const createTableTransactions = "CREATE TABLE Actions (ID INTEGER PRIMARY KEY,Timestamp TIMESTAMP NOT NULL, UserID INTEGER,ProductID  INTEGER, Credit FLOAT(4,2), Quantity INTEGER);";

//const char* const pragma = "PRAGMA page_size=512; VACUUM;";
//Products
//const char* createTableProducts = "CREATE TABLE Product (ID INTEGER PRIMARY KEY, Name VARCHAR2(30),Price NUMBER(2,1), Position NUMBER(1), isActive NUMBER(1) NOT NULL, Quantity NUMBER(2) NOT NULL);";
*/

#include <ESP8266WiFi.h>
#include <ESP8266WebServer.h>
#include <sqlite3.h>
#include <vfs.h>
#include <SPI.h>
#include <FS.h>

extern "C" {
#include "user_interface.h"
}
File db_file_obj_1;
int rc;
sqlite3* db1;
#define BufferSize 500
char tempBuffer[BufferSize];
char buffer[BufferSize];
int i;
//CONNECT TO LOCAL NETWORK
ESP8266WebServer server(80);

const char* const ssid = "Telekom-167024";
const char* const password = "fU5vLVbCFfxga";

//char* ssid = "Telekom-00E3";
//char* password = "6DKY7ELEXZ9SZ";
//open file in SPIFFS memory


void GetIndexPage()
{
    File file = SPIFFS.open("/index.html", "r");
    server.streamFile(file, "text/html");
}


void RunCommand()
{
    buffer[0] = NULL;
    String SQLCommand = server.arg("SQLCommand");

    strcat(buffer, "[");
    Serial.print("\nbuffer: ");
    Serial.print(buffer);
    const  char* persQuery = SQLCommand.c_str();
    rc = db_exec(db1, persQuery);

    if (rc != SQLITE_OK)
    {
        strcat(buffer, "]");
        server.send(200, "application/json", buffer);
        return;
    }
    int len = strlen(buffer);
    if (buffer[len - 2] == ',')
    {
        buffer[len - 2] = ']';
    }
    else
    {
        strcat(buffer, "]");
    }
    Serial.printf("buffer: %s", buffer);

    server.send(200, "application/json", buffer);

}

void LogIn()
{
    tempBuffer[0] = NULL;
    buffer[0] = NULL;
    strcat(buffer, "[");
    String UserCNP = server.arg("Username");
    String UserPassword = server.arg("Password");
    sprintf(tempBuffer, "SELECT Name from User WHERE (CNP='%s') AND (Password='%s');", UserCNP.c_str(),UserPassword.c_str());
    Serial.print("\nbuffer: ");
    Serial.print(tempBuffer);
    const  char* userQuery = tempBuffer;
    rc = db_exec(db1, userQuery);

    int len = strlen(buffer);
    if (buffer[len - 2] == ',')
    {
        buffer[len - 2] = ']';
    }
    else
    {
        strcat(buffer, "]");
    }
    Serial.printf("buffer: %s", buffer);

    if (buffer == "[]")
    {
        server.send(602, "application/json", buffer);
    }

    if (rc != SQLITE_OK)
    {
        strcat(buffer, "]");
        server.send(602, "application/json", buffer);
        return;
    }
    else {
        server.send(200, "application/json", buffer);
    }
}

//void Motor1()
//{
//    Serial.print("\nRotate motor m1");
//   // m1.Rotate(true, 200);
//    server.send(200, "text/plain", "Rotate motor 1");
//
//    for (int i = 30; i >= 0; i--)
//    {
//        lcd.clear();
//        lcd.setCursor(0, 0);
//        lcd.print("Test motor 1S");
//    }
//    lcd.clear();
//   
//}
//
//void Motor2()
//{
//    Serial.print("\nRotate motor m2");
//   // m2.Rotate(true, 200);
//
//    //m2.Rotate(false, 200);
//
//    server.send(200, "text/plain", "Rotate motor 2");
//    for (int i = 30; i >= 0; i--)
//    {
//        lcd.clear();
//        lcd.setCursor(0, 0);
//        lcd.print("Test motor 2");
//    }
//        lcd.clear();
//}
//
//void Motor3()
//{
//    Serial.print("\nRotate motor m3");
//   // m3.Rotate(false, 200);
//    server.send(200, "text/plain", "Rotate motor 3");
//    for (int i = 30; i >= 0; i--)
//    {
//        lcd.clear();
//        lcd.setCursor(0, 0);
//        lcd.print("Test motor 3");
//    }
//    lcd.clear();
//
//}
/*
void Products() {
        buffer[0] = NULL;
        strcat(buffer, "[");
        rc = db_exec(db1, "SELECT * FROM Product");
    
        int len = strlen(buffer);
        if (buffer[len - 2] == ',')
        {
            buffer[len - 2] = ']';
        }
        else
        {
            strcat(buffer, "]");
        }
        Serial.printf("buffer: %s", buffer);
        if (rc != SQLITE_OK)
        {
            strcat(buffer, "]");
            //Cannot found users
            server.send(603, "application/json", buffer);
            return;
        }
        else
        {
            server.send(200, "application/json", buffer);
        }
}*/

//void Users() {
//    buffer[0] = NULL;
//    strcat(buffer, "[");
//    rc = db_exec(db1, sqlAllUsers);
//
//    int len = strlen(buffer);
//    if (buffer[len - 2] == ',')
//    {
//        buffer[len - 2] = ']';
//    }
//    else
//    {
//        strcat(buffer, "]");
//    }
//    Serial.printf("buffer: %s", buffer);
//    if (rc != SQLITE_OK)
//    {
//        strcat(buffer, "]");
//        //Cannot found users
//        server.send(603, "application/json", buffer);
//        return;
//    }
//    else
//    {
//        server.send(200, "application/json", buffer);
//    }
//    
//}
//
//void EnableUser() {
//   
//    tempBuffer[0] = NULL;
//    buffer[0] = NULL;
//    strcat(buffer, "[");
//    String UserCNP = server.arg("CNP");
//    sprintf(tempBuffer, "UPDATE Users SET isActive = '1' WHERE CNP = %s; ", UserCNP.c_str());
//    Serial.print("\nbuffer: ");
//    Serial.print(tempBuffer);
//    const  char* userQuery = tempBuffer;
//    rc = db_exec(db1, userQuery);
//    if (rc != SQLITE_OK)
//    {
//        strcat(buffer, "]");
//        server.send(200, "application/json", buffer);
//        return;
//    }
//    int len = strlen(buffer);
//    if (buffer[len - 2] == ',')
//    {
//        buffer[len - 2] = ']';
//    }
//    else
//    {
//        strcat(buffer, "]");
//    }
//    server.send(200, "application/json", buffer);
//
//}
//
//void DisableUser()
//{
//
//    tempBuffer[0] = NULL;
//    buffer[0] = NULL;
//    strcat(buffer, "[");
//    String UserCNP = server.arg("CNP");
//    sprintf(tempBuffer, "UPDATE Users SET isActive = '0' WHERE CNP = %s; ", UserCNP.c_str());
//    Serial.print("\nbuffer: ");
//    Serial.print(tempBuffer);
//    const  char* userQuery = tempBuffer;
//    rc = db_exec(db1, userQuery);
//    if (rc != SQLITE_OK)
//    {
//        strcat(buffer, "]");
//        server.send(200, "application/json", buffer);
//        return;
//    }
//    int len = strlen(buffer);
//    if (buffer[len - 2] == ',')
//    {
//        buffer[len - 2] = ']';
//    }
//    else
//    {
//        strcat(buffer, "]");
//    }
//    server.send(200, "application/json", buffer);
//
//}
//
//void EditUser() {
//    tempBuffer[0] = NULL;
//    buffer[0] = NULL;
//    strcat(buffer, "[");
//    String UserCNP = server.arg("CNP");
//    String NewFirstName = server.arg("toEditFirstName");
//    String NewLastName = server.arg("toEditLastName");
//    String NewPassword = server.arg("toEditPassword");
//    String NewCredit = server.arg("toEditCredit");
//    String NewIsAdmin = server.arg("toEditAdmin");
//    String NewTagNumber = server.arg("toEditTagNumber");
//    sprintf(tempBuffer, "UPDATE Users SET FirstName = '%s', LastName = '%s', Password = '%s', Credit = '%s', IsAdmin = '%s', TagNumber = '%s' WHERE CNP = '%s'; ", NewFirstName.c_str(), NewLastName.c_str(), NewPassword.c_str(), NewCredit.c_str(), NewIsAdmin.c_str(), NewTagNumber.c_str(), UserCNP.c_str());
//    Serial.print("\nbuffer: ");
//    Serial.print(tempBuffer);
//    const  char* EditUserQuery = tempBuffer;
//    rc = db_exec(db1, EditUserQuery);
//    if (rc != SQLITE_OK)
//    {
//        strcat(buffer, "]");
//        server.send(605, "application/json", buffer);
//        return;
//    }
//    else
//    {
//        int len = strlen(buffer);
//        if (buffer[len - 2] == ',')
//        {
//            buffer[len - 2] = ']';
//        }
//        else
//        {
//            strcat(buffer, "]");
//        }
//        server.send(200, "application/json", buffer);
//        
//    }
//
//}
//
//void AddUser() {
//    tempBuffer[0] = NULL;
//    buffer[0] = NULL;
//    strcat(buffer, "[");
//
//    String UserCNP = server.arg("AddCNP");
//    String FirstName = server.arg("AddFirstName");
//    String LastName = server.arg("AddLastName");
//    String Password = server.arg("AddPassword");
//    String IsAdmin = server.arg("CheckIfAdmin");
//    String TagNumber = server.arg("AddTagNumber");
//
//    sprintf(tempBuffer, "INSERT INTO Users(CNP, FirstName, LastName, Password, Credit, TagNumber, IsAdmin, IsActive) VALUES(%s, '%s', '%s', '%s', 0, '%s', %s, 1);", UserCNP.c_str(), FirstName.c_str(), LastName.c_str(), Password.c_str(), TagNumber.c_str(), IsAdmin.c_str());
//    Serial.print("\nbuffer: ");
//    Serial.print(tempBuffer);
//    const  char* EditUserQuery = tempBuffer;
//    rc = db_exec(db1, EditUserQuery);
//    if (rc != SQLITE_OK)
//    {
//        strcat(buffer, "]");
//        server.send(605, "application/json", buffer);
//        return;
//    }
//    else
//    {
//        int len = strlen(buffer);
//        if (buffer[len - 2] == ',')
//        {
//            buffer[len - 2] = ']';
//        }
//        else
//        {
//            strcat(buffer, "]");
//        }
//        server.send(200, "application/json", buffer);
//
//    }
//}

const char* const jsonUser = "{\"CNP\":%s, \"FirstName\": \"%s\", \"LastName\":\"%s\", \"isAdmin\": %s, \"Credit\": %s,\"TagNumber\": \"%s\", \"isActive\": %s}";

const char* const data = "Callback function called";
static int callback(void* data, int argc, char** argv, char** azColName)
{

    strcat(buffer, "{");
    tempBuffer[0] = NULL;
    for (i = 0; i < argc; i++)
    {
        if (i == argc - 1)
        {
            sniprintf(tempBuffer, 50, "\"%s\": \"%s\"", azColName[i], argv[i] ? argv[i] : "NULL");
        }
        else
        {
            sniprintf(tempBuffer, 50, "\"%s\": \"%s\", ", azColName[i], argv[i] ? argv[i] : "NULL");
        }
        strcat(buffer, tempBuffer);
    }
    strcat(buffer, "}, ");

    return 0;
}


int db_open(const char* filename, sqlite3** db)
{
    int rc = sqlite3_open(filename, db);
    if (rc)
    {
        Serial.printf("Can't open database: %s\n", sqlite3_errmsg(*db));
        return rc;
    }
    else
    {
        Serial.printf("Opened database successfully\n");
    }
    return rc;
}

char* zErrMsg = 0;
int db_exec(sqlite3* db, const char* sql)
{
    Serial.print("\nPrinting SQL: ");
    Serial.print(sql);
    Serial.print("\n");


    Serial.println("\ndb_exec");
    int rc = sqlite3_exec(db, sql, callback, (void*)data, &zErrMsg);

    if (rc != SQLITE_OK)
    {
        Serial.printf("SQL error: %s\n", zErrMsg);
        for (int i = 0; i < strlen(zErrMsg); i++)
        {
            if (zErrMsg[i] == '\"')
            {
                zErrMsg[i] = '\'';
            }
        }
        strcat(buffer, "{ \"ErrorText\": \"");
        strcat(buffer, zErrMsg);
        strcat(buffer, "\"}");
        sqlite3_free(zErrMsg);
    }
    else
    {
        Serial.printf("Operation done successfully\n");
    }
    return rc;
}

void setup()
{
    system_update_cpu_freq(SYS_CPU_160MHZ);

    Serial.begin(115200);
    Serial.println("Starting...");
    SPIFFS.begin();

    WiFi.begin(ssid, password);

    while (WiFi.status() != WL_CONNECTED)
    {
        Serial.print(".");
        delay(500);
    }
    Serial.println("");
    Serial.print("IP Address: ");
    Serial.println(WiFi.localIP());

    if (!SPIFFS.begin())
    {
        Serial.println("Failed to mount file system");
        return;
    }
    // see all files in SPIFFS memory   
    Dir dir = SPIFFS.openDir("");
    while (dir.next())
    {
        Serial.println(dir.fileName());
        Serial.println(dir.fileSize());
    }
    // remove existing file
    //SPIFFS.remove("/test1.db");
    SPIFFS.remove("/ico.ico");
    SPIFFS.remove("/VendingMachineDB.db");

    sqlite3_initialize();

    // Open databases
    vfs_set_spiffs_file_obj(&db_file_obj_1);
    if (db_open("/FLASH/vm.db", &db1))
        return;
        
         //Create table Transactions
    rc = db_exec(db1, "SELECT * FROM User;");
    if (rc != SQLITE_OK)
    {
        sqlite3_close(db1);
        return;
    }

/*
            //Create table User
    rc = db_exec(db1, "CREATE TABLE Users (CNP INTEGER PRIMARY KEY, FirstName VARCHAR2(16), LastName VARCHAR2(16), Password VARCHAR2(12) NOT NULL, TagNumber VARCHAR2(16), Credit NUMBER(4,2) NOT NULL, IsAdmin NUMBER(1) NOT NULL, IsActive NUMBER(1) NOT NULL);");
    if (rc != SQLITE_OK)
    {
        sqlite3_close(db1);
        return;
    }

 //Create table Transactions
    rc = db_exec(db1, "CREATE TABLE Action(ID INTEGER PRIMARY KEY, Timestamp TIMESTAMP NOT NULL, TypeID NUMBER(1) NOT NULL, Credit NUMBER(4,2), Quantity NUMBER(2));");
    if (rc != SQLITE_OK)
    {
        sqlite3_close(db1);
        return;
    }

    //Create table Products
    rc = db_exec(db1, "CREATE TABLE Product (ID INTEGER PRIMARY KEY, Name VARCHAR2(30),Price NUMBER(2,1), Position NUMBER(1), isActive NUMBER(1) NOT NULL, Quantity NUMBER(2) NOT NULL);");
    if (rc != SQLITE_OK)
    {
        sqlite3_close(db1);
        return;
    }

    //Insert user into table
    rc = db_exec(db1, "INSERT INTO Users (CNP, FirstName, LastName, Password, Credit, isAdmin, isActive) VALUES (19712073264,'Ion', 'Vasilescu', 'abc', 4.85, 1, 1);");
    if (rc != SQLITE_OK)
    {
        sqlite3_close(db1);
        return;
    }

    //Insert user into table
    rc = db_exec(db1, "INSERT INTO Users (CNP, FirstName, LastName, Password, Credit, isAdmin, isActive) VALUES  (1, 'Anonymus', 'Anonymus', '1', 0, 0, 1 );");
    if (rc != SQLITE_OK)
    {
        sqlite3_close(db1);
        return;
    }
   */
    //m3.Rotate(false, 200);
   
    //for removing files use he commend bellow
    //SPIFFS.remove("/index.htm");

    server.on("/", GetIndexPage);
    server.on("/LogIn", LogIn);
    //server.on("/Motor1", Motor1);
    //server.on("/Motor2", Motor2);
    //server.on("/Motor3", Motor3);
    server.on("/RunCommand", RunCommand);
    //server.on("/Users", Users);
    //server.on("/EnableUser", EnableUser);
    //server.on("/DisableUser", DisableUser);
    //server.on("/EditUser", EditUser);
    //server.on("/AddUser", AddUser);
    //server.on("/Products", Products);
    server.begin();

}
void loop()
{
    server.handleClient();
}

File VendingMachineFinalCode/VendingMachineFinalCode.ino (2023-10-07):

/*
 Name:		VendingMachineFinalCode.ino
 Created:	5/17/2022 1:21:05 PM
 Author:	Cozinia
*/

// the setup function runs once when you press reset or power the board


#include "RFID.h"
#include "CoinAcceptor.h"
#include "ActionOnMotors.h"
#include <LiquidCrystal_I2C.h>
#include "Functions.h"
#include <SPI.h>
#include <FS.h>
#include <ESP8266WiFi.h>
#include <ESP8266WebServer.h>
#include "WebServer.h"
#include "FileDb.h"
#include "ActionOnMotors.h"
#include "CoinAcceptor.h"
const char* const ssid = "iPhone 11";
const char* const password = "aeronautic";



void InitWiFi()
{
	Serial.println("\nConnecting to the WiFi");
	WiFi.mode(WIFI_STA);
	WiFi.begin(ssid, password);
	Serial.println("Waiting for connection");
	while (WiFi.status() != WL_CONNECTED)
	{
		delay(500);
		Serial.print(".");
	}
	Serial.println("");
	Serial.print("Connected to ");
	Serial.println(ssid);
	Serial.print("IP address: ");
	Serial.println(WiFi.localIP());
}


void setup() {
	Serial.begin(115200);
	SPIFFS.begin();
	unsigned long StartTime = millis();
	InitWiFi();
	WebServer__Init();
	fileDb.init();
	fileDb.InitData();
	ActionOnMotors_Init();
	RFID_Init();
	lcd.clear();
		lcd.setCursor(0, 0);
		lcd.print("Please wait...");
		pcf8574_Button.digitalWrite(FixPin, LOW);
		//pcf8574_Button.digitalWrite(FixPin, 0);
	OpenDoor();
	CoinAcceptor_Init();
	lcd.clear();
}

// the loop function runs over and over again until power down or reset
void loop() {
	WebServer__Process();
	ActionOnMotors_Process();
	CoinAcceptor_Process();
	RFID_Process();
	server.handleClient();
	
}

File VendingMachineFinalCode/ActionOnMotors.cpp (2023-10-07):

// 
// 
// 

#include "ActionOnMotors.h"
using namespace System;


PCF8574 pcf8574(0x21);
const int DirXPin = P0;
const int StepXPin = P1;

const int DirYPin = P2;
const int StepYPin = P3;

const int DirZPin = P4;
const int StepZPin = P5;

const int DirAPin = P6;
const int StepAPin = P7;

PCF8574 pcf8574_Button(0x20);
const int  EnPin = P6;
const int Button1 = P0;
const int Button2 = P1;
const int Button3 = P2;
const int Button4 = P3;
const int RelayPin = P5;
const int FixPin = P7;
const int UserLogOutButton = P4;
extern float credit;

LiquidCrystal_I2C lcd(0x27, 16, 2);
char MyBuffer[BufferSize];
char TempBuffer[BufferSize];


void SetPcfPin(int pin, int value)
{

    if (pin == EnPin)
    {
        pcf8574_Button.digitalWrite(pin, value);
    }
    else
    {
        pcf8574.digitalWrite(pin, value);
    }

}

Motor m1(EnPin, DirXPin, StepXPin, SetPcfPin);
Motor m2(EnPin, DirYPin, StepYPin, SetPcfPin);
Motor m3(EnPin, DirZPin, StepZPin, SetPcfPin);
Motor m4(EnPin, DirAPin, StepAPin, SetPcfPin);


int Button1_Get()
{
	int pinValue = !pcf8574_Button.digitalRead(Button1);
	//Serial.println(pinValue);
	return pinValue;
}
int Button2_Get()
{
	int pinValue = !pcf8574_Button.digitalRead(Button2);
	//Serial.println(pinValue);
	return pinValue;
}
int Button3_Get()
{
	int pinValue = !pcf8574_Button.digitalRead(Button3);
	//Serial.println(pinValue);
	return pinValue;
}
int Button4_Get()
{
	int pinValue = !pcf8574_Button.digitalRead(Button4);
	//Serial.println(pinValue);
	return pinValue;
}
int UserLogOutButton_Get()
{
	int pinValue = !pcf8574_Button.digitalRead(UserLogOutButton);
	//Serial.println(pinValue);
	return pinValue;
}

void Button1_product();
void Button2_product();
void Button3_product();
void Button4_product();

Button b1(Button1_Get);
Button b2(Button2_Get);
Button b3(Button3_Get);
Button b4(Button4_Get);
Button b5(UserLogOutButton_Get);

void Button1_Down(Button* sender)
{
	Serial.println("Down");

	Button1_product();


}
void Button2_Down(Button* sender)
{
	Serial.println("Down");
	Button2_product();

}
void Button3_Down(Button* sender)
{
	Serial.println("Down");
	Button3_product();

}
void Button4_Down(Button* sender)
{
	Serial.println("Down");
	Button4_product();

}
void Button5_Down(Button* sender)
{
	Serial.println("UserLogOff");
	credit = 0;

}

void ActionOnMotors_Init() {
    pcf8574.pinMode(StepXPin, OUTPUT);
    pcf8574.pinMode(DirXPin, OUTPUT);
    pcf8574.pinMode(StepYPin, OUTPUT);
    pcf8574.pinMode(DirYPin, OUTPUT);
    pcf8574.pinMode(StepZPin, OUTPUT);
    pcf8574.pinMode(DirZPin, OUTPUT);
    pcf8574.pinMode(StepAPin, OUTPUT);
    pcf8574.pinMode(DirAPin, OUTPUT);

    pcf8574_Button.pinMode(EnPin, OUTPUT);
    pcf8574_Button.pinMode(Button1, INPUT_PULLUP);
    pcf8574_Button.pinMode(Button2, INPUT_PULLUP);
    pcf8574_Button.pinMode(Button3, INPUT_PULLUP);
    pcf8574_Button.pinMode(Button4, INPUT_PULLUP);
	pcf8574_Button.pinMode(UserLogOutButton, INPUT_PULLUP);
	pcf8574_Button.pinMode(RelayPin, OUTPUT);
	pcf8574_Button.pinMode(FixPin, OUTPUT);
	pcf8574_Button.digitalWrite(RelayPin, LOW);
	pcf8574_Button.digitalWrite(FixPin, HIGH);

    lcd.init();
    lcd.backlight();
    lcd.setBacklight(HIGH);

	b1.EventDown = Button1_Down;
	b2.EventDown = Button2_Down;
	b3.EventDown = Button3_Down;
	b4.EventDown = Button4_Down;
	b5.EventDown = Button5_Down;

    //Print on screen to check if sending data to pcf8574
    if (pcf8574.begin())
    {
        Serial.println(":\n Sending data to PCF8574.");
    }
    else
    {
        Serial.println("Error while sending data to PCF8574.");
    }

    //Print on screen to check if sending data to pcf8574
    if (pcf8574_Button.begin())
    {
        Serial.println(":\n Sending data to PCF8574.");
    }
    else
    {
        Serial.println("Error while sending data to PCF8574.");
    }

        lcd.clear();
        lcd.setCursor(0, 0);
        lcd.print("Please wait");

   // m1.Rotate(true, 400);
}

void Motor1()
{
    Serial.print("\nRotate motor m1");
    m1.Rotate(true, 400);
    lcd.clear();

    for (int i = 100; i >= 0; i--)
    {
        lcd.setCursor(0, 0);
        lcd.print("Test motor 1");
    }
    lcd.clear();
    server.send(200, "text/plain", "Rotate motor 1");
   
}

void Motor2()
{
    Serial.print("\nRotate motor m2");
    m2.Rotate(true, 400);
    lcd.clear();

    for (int i = 100; i >= 0; i--)
    {
        lcd.setCursor(0, 0);
        lcd.print("Test motor 2");
    }
    lcd.clear();
    server.send(200, "text/plain", "Rotate motor 2");
}

void Motor3()
{
    Serial.print("\nRotate motor m3");
    m3.Rotate(true, 400);
    lcd.clear();

    for (int i = 100; i >= 0; i--)
    {
        lcd.setCursor(0, 0);
        lcd.print("Test motor 3");
    }
    lcd.clear();
    server.send(200, "text/plain", "Rotate motor 3");
}

void Motor4()
{
    Serial.print("\nRotate motor m4");
    m4.Rotate(false, 400);
    lcd.clear();

    for (int i = 100; i >= 0; i--)
    {
        lcd.setCursor(0, 0);
        lcd.print("Test motor 4");
    }
    lcd.clear();
    server.send(200, "text/plain", "Rotate motor 4");
}

void OpenDoor() {
	unsigned long Time = millis();
	
	while (millis() - Time <= 1000) {
		pcf8574_Button.digitalWrite(RelayPin, LOW);
		pcf8574_Button.digitalWrite(FixPin, LOW);
		
	}
	pcf8574_Button.digitalWrite(RelayPin, HIGH);
	delay(100);
	pcf8574_Button.digitalWrite(FixPin, LOW);
	server.send(200);
}

void Button_Up(Button* sender)
{
	Serial.println("Up");
}


void Button1_product()
{

	if (credit >= 1.00)
	{
		credit = credit - 1.00;

		fileDb.products[0].Quantity = fileDb.products[0].Quantity - 1;

		m1.Rotate(true, 400);
		lcd.clear();
		for (int i = 30; i >= 0; i--)
		{
			lcd.setCursor(1, 0);
			lcd.print("item selected:");
			lcd.setCursor(3, 1);
			lcd.print("Snikers");
		}
		lcd.clear();
		lcd.setCursor(0, 0);
		lcd.print("Credit:");
		lcd.setCursor(7, 0);
		lcd.print(credit);
	}
	else
	{
		lcd.clear();
		lcd.setCursor(0, 0);
		lcd.print("Not enough ");
		lcd.setCursor(0, 1);
		lcd.print("credit");
	}

}

void Button2_product()
{
	if (credit >= 1.50)
	{
		credit = credit - 1.50;
		fileDb.products[1].Quantity = fileDb.products[0].Quantity - 1;
		m2.Rotate(true, 400);
		lcd.clear();
		for (int i = 30; i >= 0; i--)
		{
			lcd.setCursor(1, 0);
			lcd.print("item selected:");
			lcd.setCursor(3, 1);
			lcd.print("Mars");
		}
		lcd.clear();
		lcd.setCursor(0, 0);
		lcd.print("Credit:");
		lcd.setCursor(7, 0);
		lcd.print(credit);

	}
	else
	{
		lcd.clear();
		lcd.setCursor(0, 0);
		lcd.print("Not enough ");
		lcd.setCursor(0, 1);
		lcd.print("credit");
	}
}
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

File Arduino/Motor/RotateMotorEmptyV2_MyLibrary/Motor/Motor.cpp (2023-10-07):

#include "Motor.h"


namespace System
{

	Motor::Motor(int enPin, int dirPin, int stepPin, SetPinFunc setPin)
	{
		this->enPin = enPin;
		this->dirPin = dirPin;
		this->stepPin = stepPin;
		this->setPinFunc = setPin;

		steps = 0;

		rotateTime = 0;
	}

	void Motor::Rotate(bool dir, int steps)
	{
		Serial.println("Rotate");
		this->steps = steps * 2;
		setPinFunc(enPin, LOW);
		setPinFunc(dirPin, dir);

	}

	void Motor::Cancel()
	{
		steps = 0;
		setPinFunc(enPin, HIGH);
		Serial.println("Cancel() entered");

	}

	void Motor::Process()
	{
		if (steps)
		{

			//Serial.println("steps");
			if (millis() - rotateTime >= MOTOR_WAIT_INTERVAL)
			{

				if ((steps % 2) == 0)
				{
					setPinFunc(stepPin, HIGH);
					//Serial.println(steps);

				}
				else
				{
					setPinFunc(stepPin, LOW);
				}
				rotateTime = millis();
				steps--;

				if (!steps)
					Cancel();
			}

		}




	}


}
